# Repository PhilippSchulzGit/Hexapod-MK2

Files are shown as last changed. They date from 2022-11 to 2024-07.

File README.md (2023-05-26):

# Hexapod_MK2
CAD and Code for my second iteration of a hexapod robot.

Check the video on YouTube for more detailed information: https://youtu.be/Rfa3LTjmms0

Update 2023:
This repository also contains the program files for the inverse kinematic model in its own sub folder. Video: https://youtu.be/MJIe1nkX_Xk

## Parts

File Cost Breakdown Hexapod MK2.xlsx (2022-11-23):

Category | Part | Time | Filament [g] | Count | Price | Sum
 |  |  |  |  |  |  | time | filament | price
3D Prints | TorsoV1 | 11:51:00 | 64 | 1 | 1.88 € | 6.28 € | 0.49375 | 64 | 1.88
 | TorsoServoMountV1 | 4:19:00 | 25 | 6 | 0.10 € |  | 1.079166667 | 150 | 0.62
 | LegHipV2 | 11:06:00 | 84 | 6 | 0.35 € |  | 2.775 | 504 | 2.08
 | LegMiddleV1 | 6:31:00 | 27 | 6 | 0.11 € |  | 1.629166667 | 162 | 0.66
 | LegTipV1 | 7:09:00 | 42 | 6 | 0.17 € |  | 1.7875 | 252 | 1.04
Electronics | 9g Servo (https://www.amazon.de/gp/product/B07KFXYDHF/) | - | - | 18 | 1.75 € | 82.14 € |  |  | 31.5
 | PCA 9685 PWM Board (https://www.amazon.de/gp/product/B07CRDCP8V/) | - | - | 1 | 3.33 € |  |  |  | 3.33
 | RC Servo Cable Extensions (https://www.amazon.de/gp/product/B082Y4QK9J/) | - | - | 1 | 9.99 € |  |  |  | 9.99
 | ESP 8266 NodeMCU V2 (https://www.amazon.de/dp/B06Y1LZLLY/) | - | - | 1 | 7.49 € |  |  |  | 7.49
 | GY-521 MPU-6050 (https://www.amazon.de/gp/product/B07TKLYBD6/) | - | - | 1 | 4.79 € |  |  |  | 4.79
 | Mini 360 Buck Converter (https://www.amazon.de/gp/product/B07DK64L2J/) | - | - | 4 | 1.50 € |  |  |  | 5.99
 | 3S 11,1V 2200mAh LiPo Battery (https://www.amazon.de/gp/product/B07LFSPQM2/) | - | - | 1 | 19.05 € |  |  |  | 19.05
 |  |  |  |  | Sum | 88.42 €

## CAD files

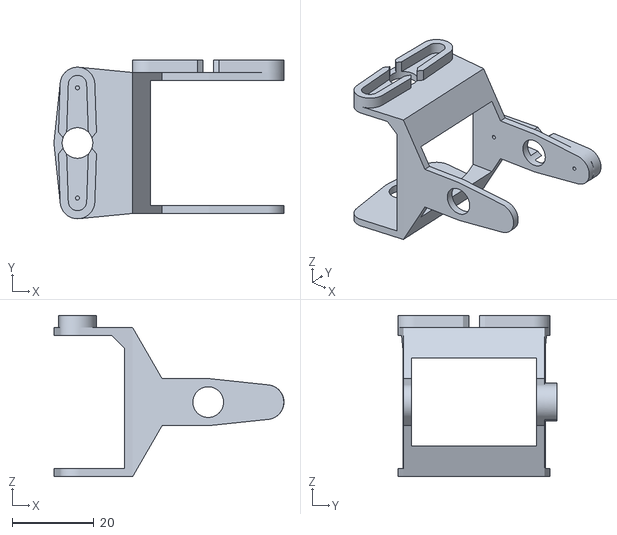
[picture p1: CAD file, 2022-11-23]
CAD/LegHipV2.stl
56.3 x 38.8 x 39.5

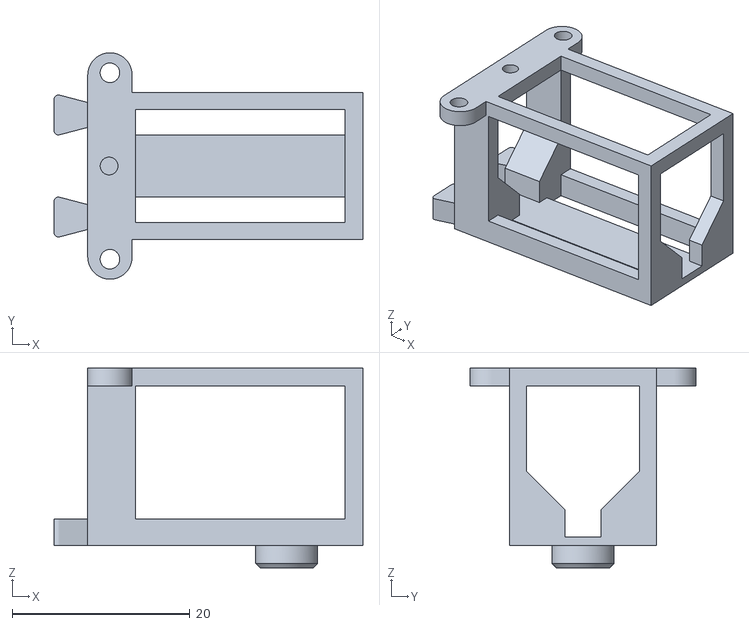
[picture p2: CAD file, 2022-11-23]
CAD/TorsoServoMountV1.stl
34.8 x 25.5 x 22.5

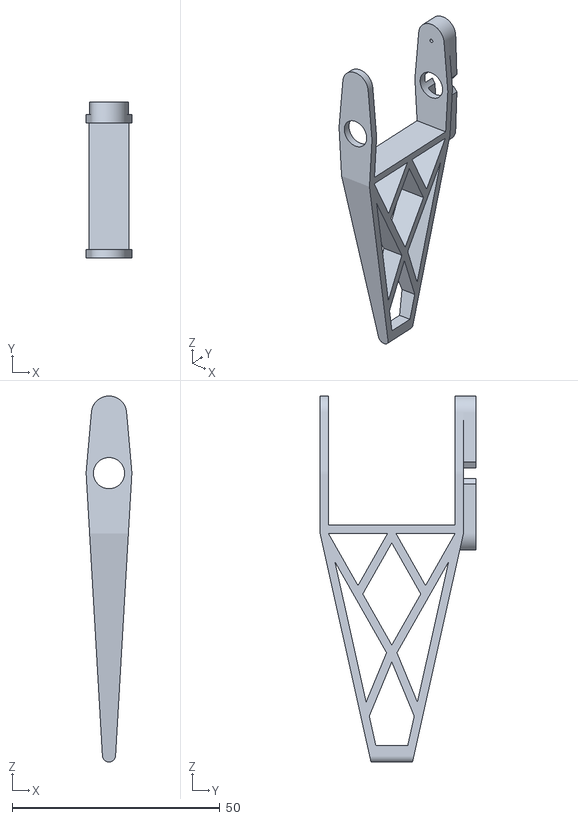
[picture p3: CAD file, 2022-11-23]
CAD/LegTipV1.stl
11.0 x 37.5 x 88.1

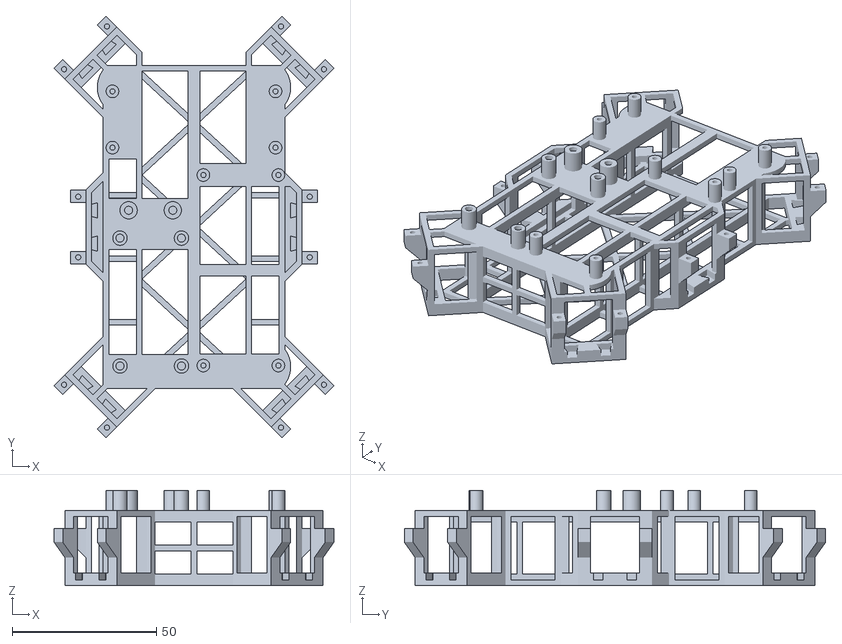
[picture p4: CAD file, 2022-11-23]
CAD/TorsoV1.stl
97.0 x 146.0 x 33.0

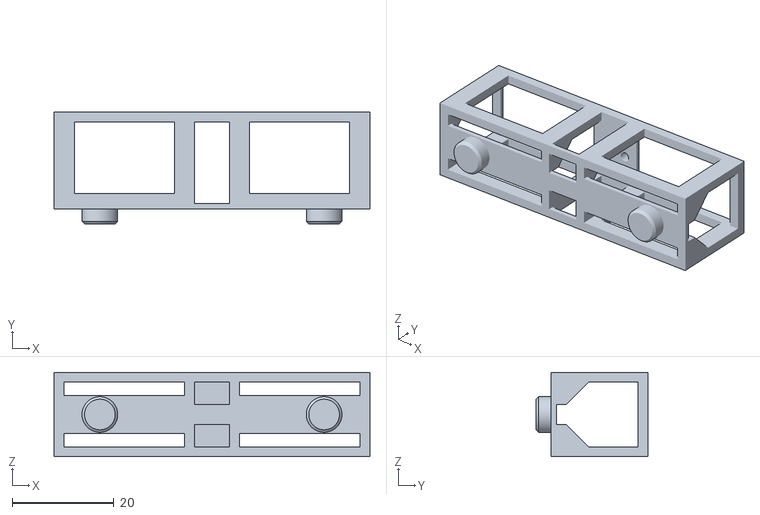
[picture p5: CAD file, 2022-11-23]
CAD/LegMiddleV1.stl
62.0 x 22.0 x 16.5

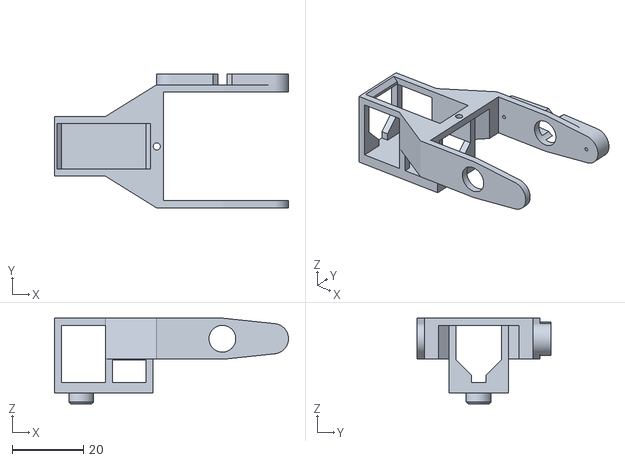
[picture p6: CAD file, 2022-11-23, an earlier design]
CAD/LegHipV1.stl
65.6 x 37.5 x 24.0

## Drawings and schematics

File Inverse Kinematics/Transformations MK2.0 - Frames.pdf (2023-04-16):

# Transformation MK2.0 - Frames

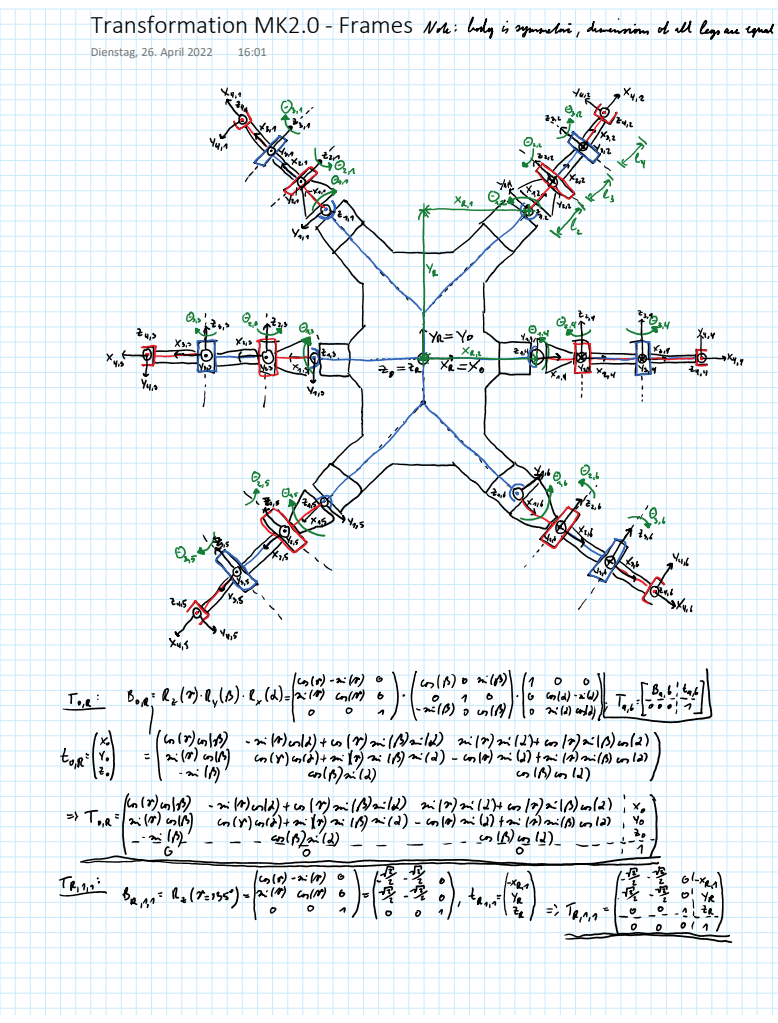
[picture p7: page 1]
Dienstag, 26. April 2022

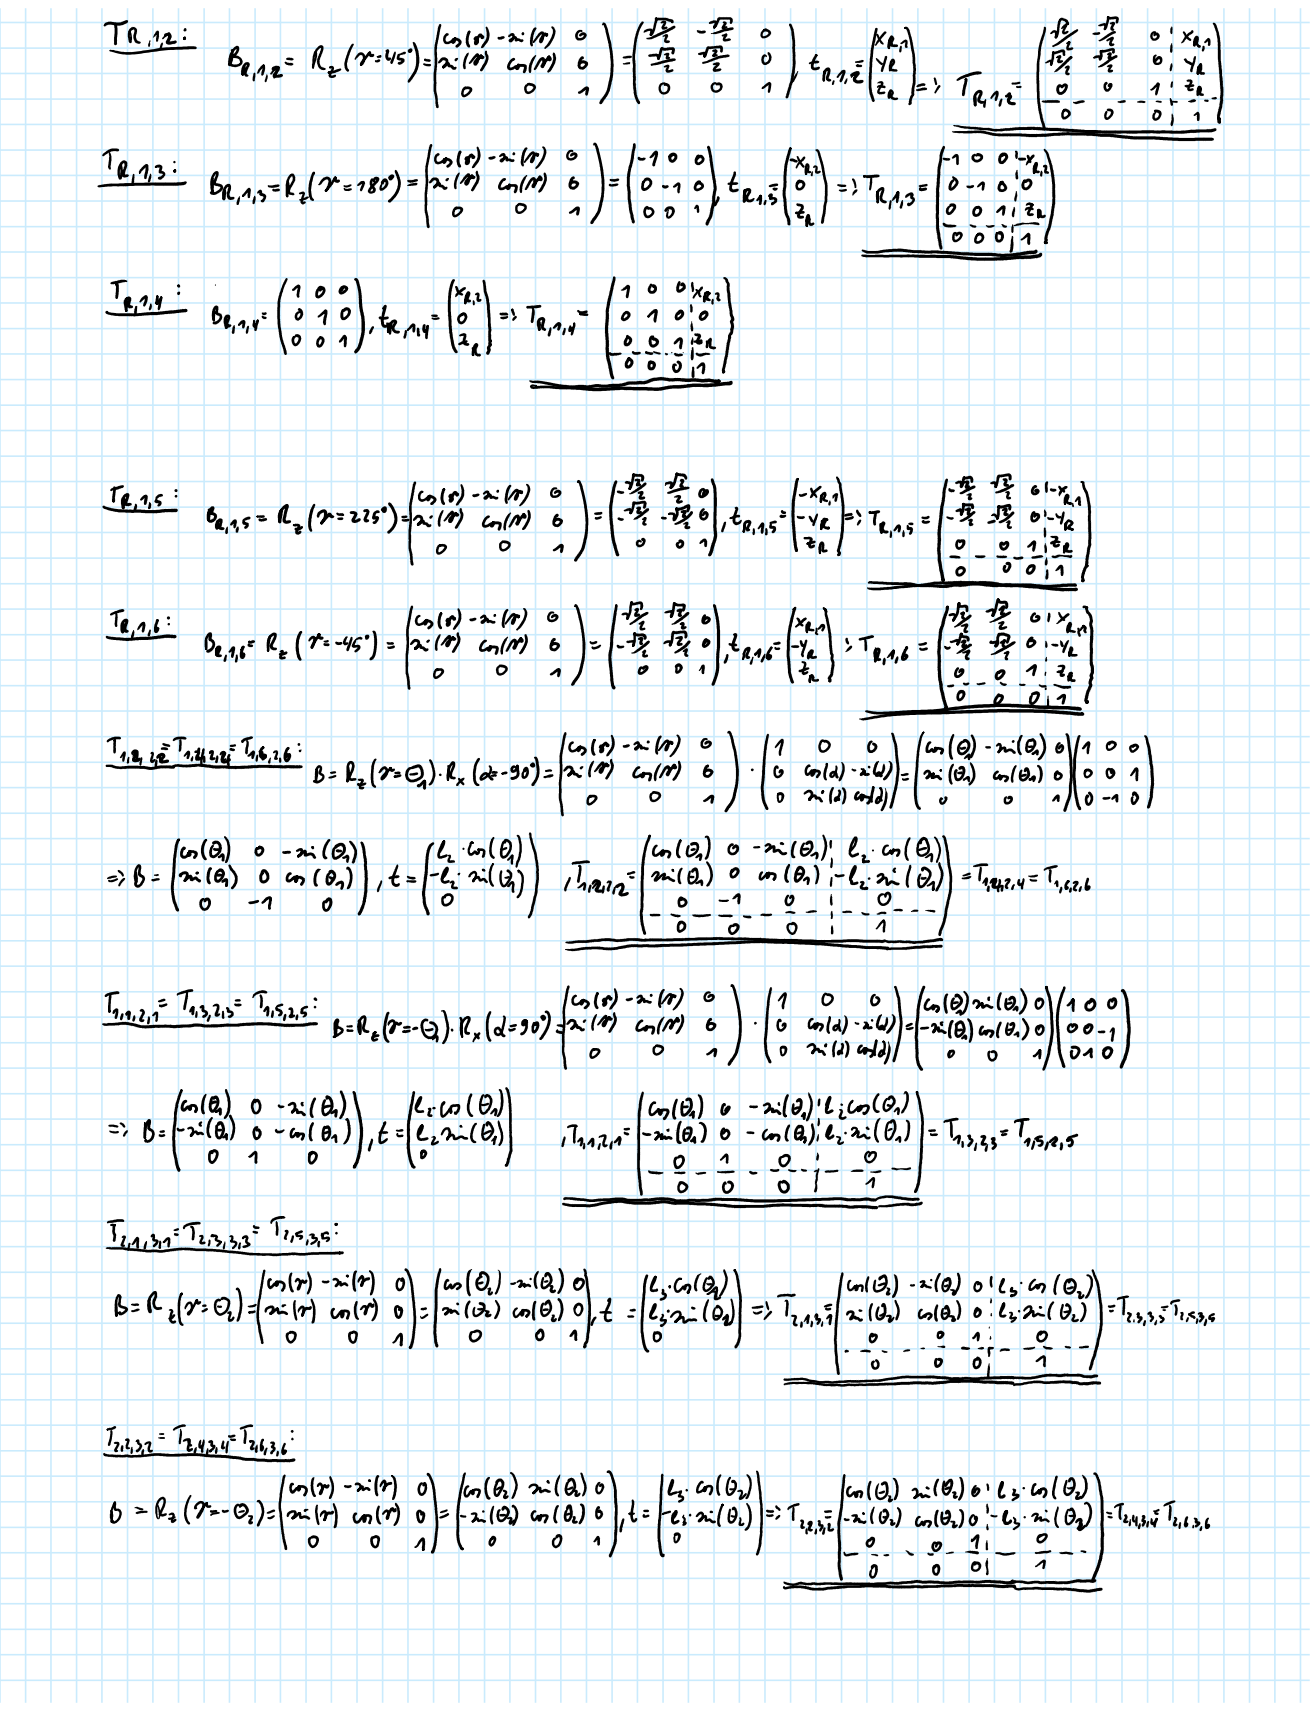
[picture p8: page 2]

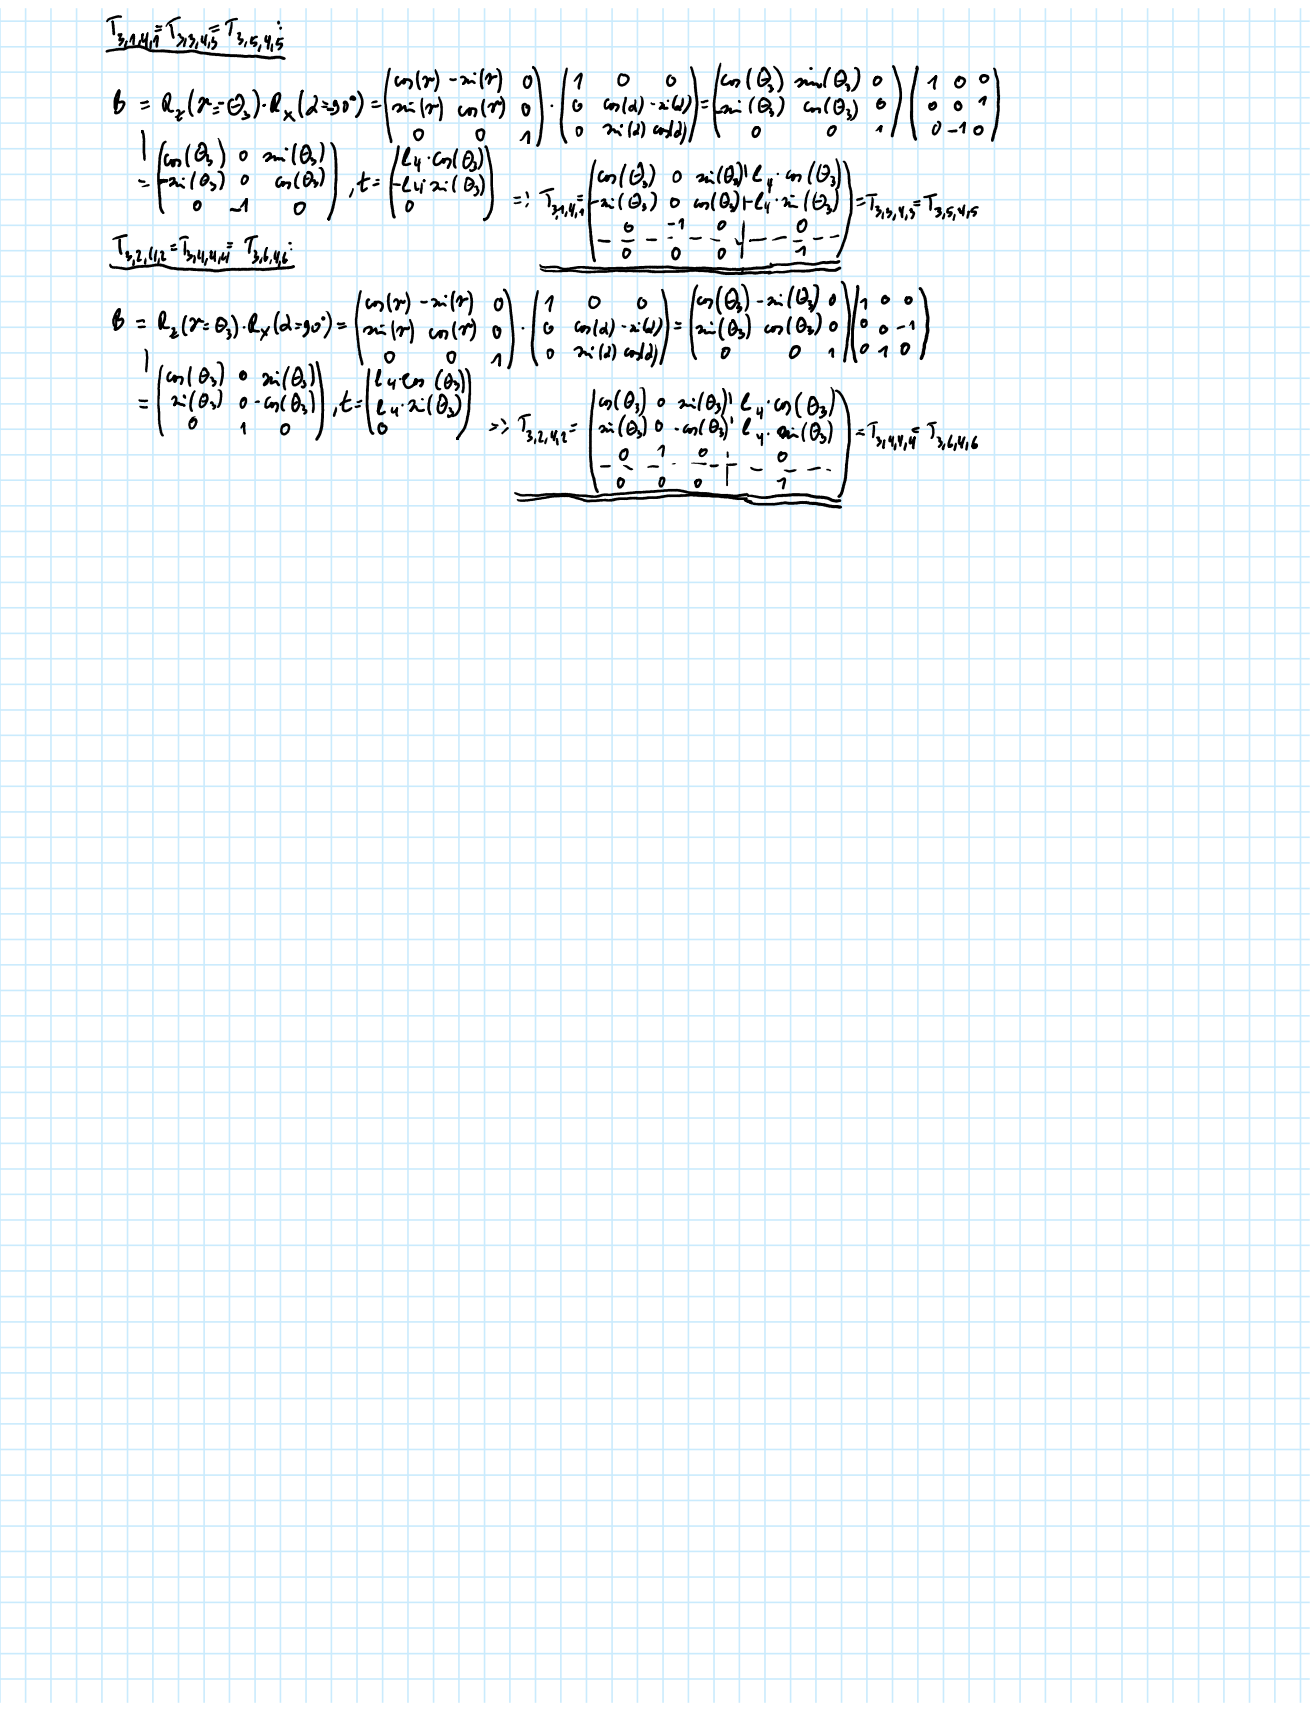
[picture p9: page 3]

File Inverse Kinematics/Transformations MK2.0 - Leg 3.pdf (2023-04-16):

# Transformation MK2.0 - Leg 3

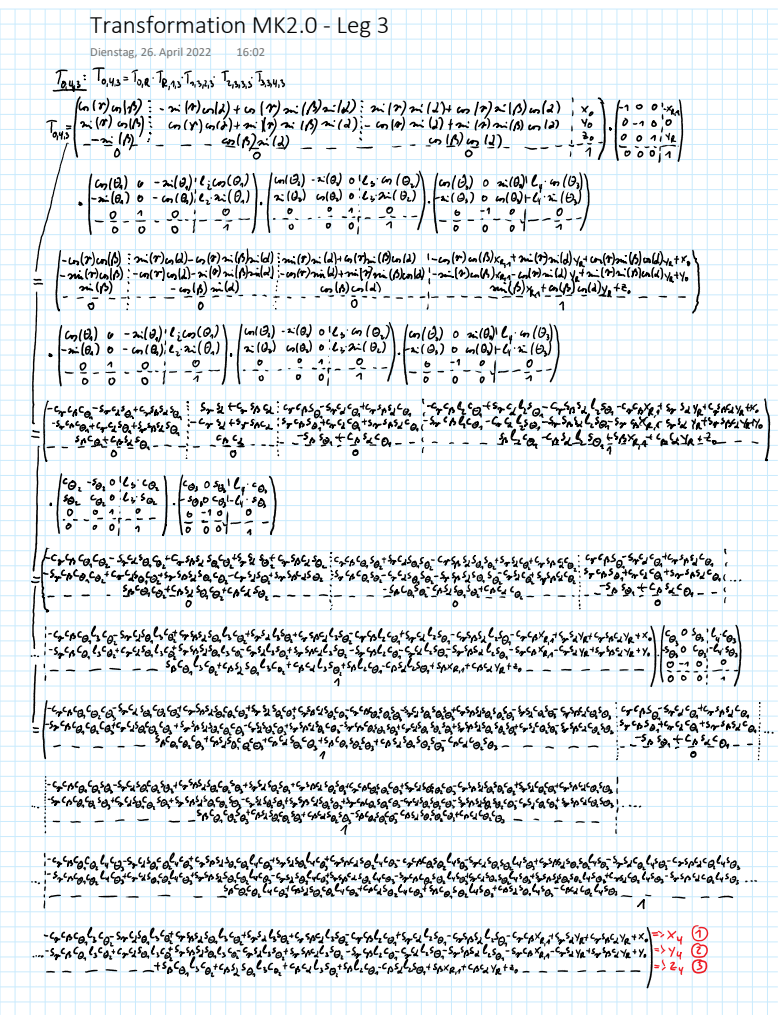
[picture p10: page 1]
Dienstag, 26. April 2022

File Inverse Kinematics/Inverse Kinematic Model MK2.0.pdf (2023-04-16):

# IKM MK2.0

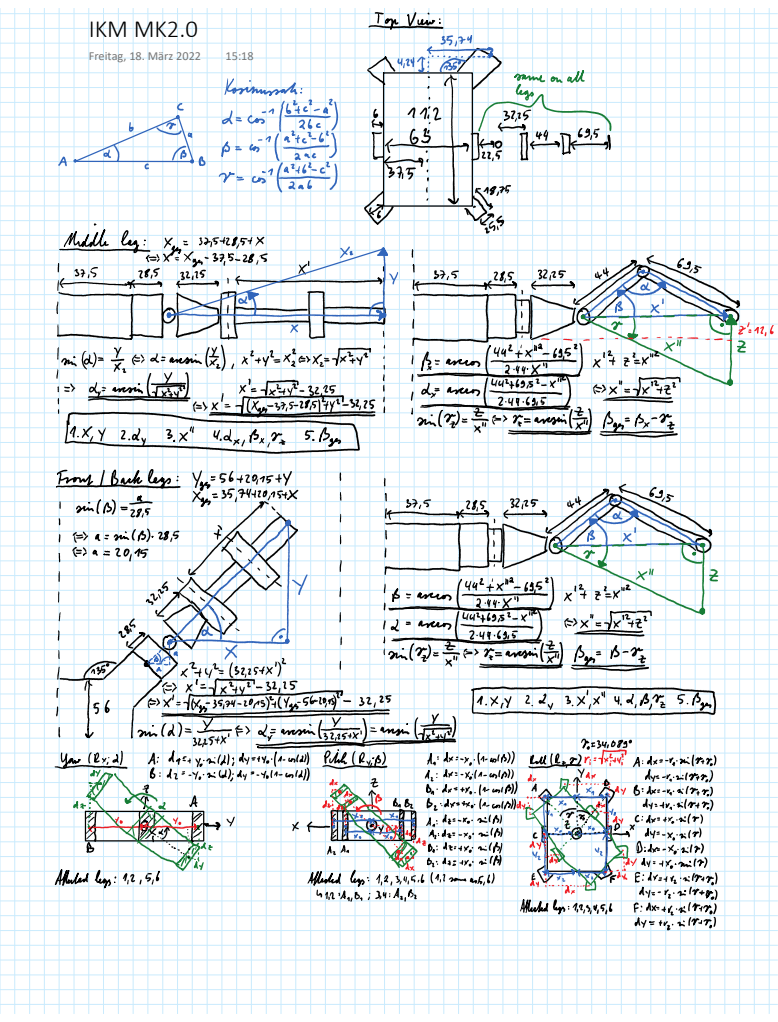
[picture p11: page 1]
Freitag, 18. März 2022

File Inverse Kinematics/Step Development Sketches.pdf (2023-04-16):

# Step Development Sketches

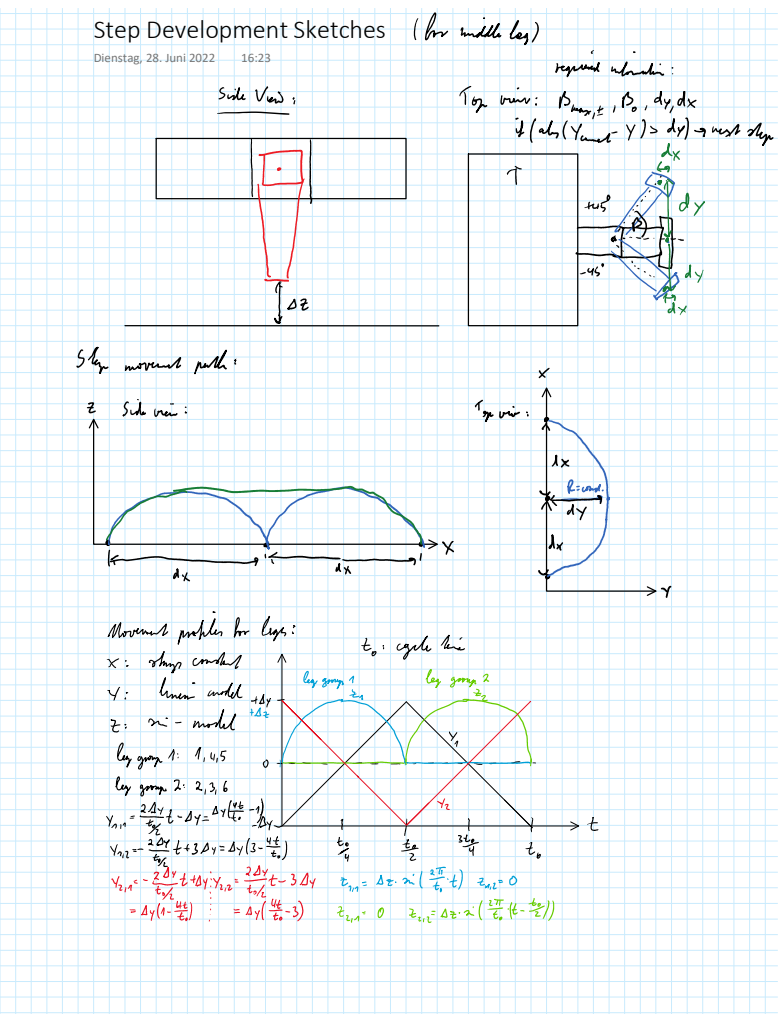
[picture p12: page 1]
Dienstag, 28. Juni 2022

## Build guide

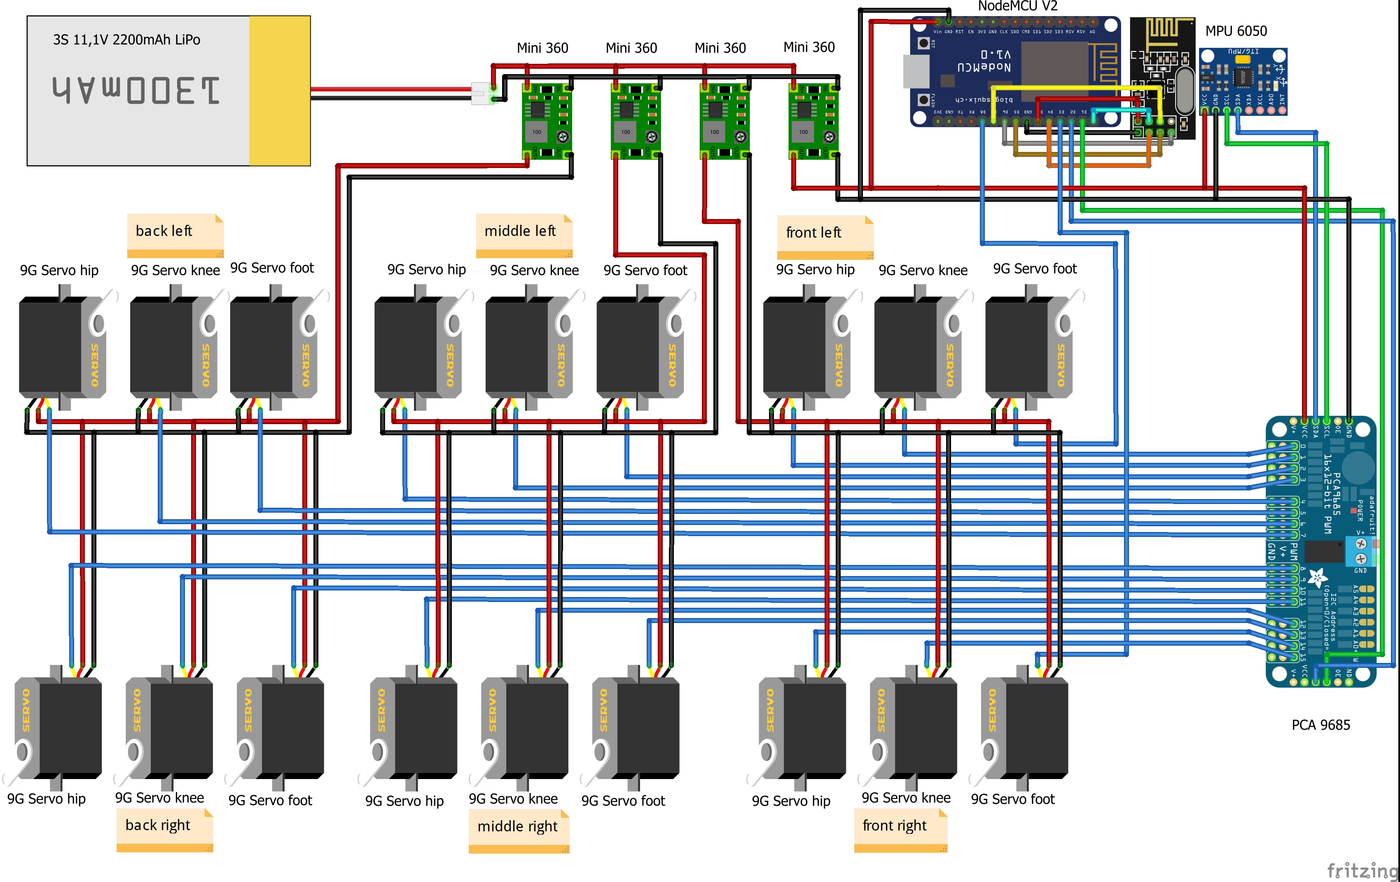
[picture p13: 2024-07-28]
Electrical Documents/Hexapod MK2 Wiring Diagram.jpg

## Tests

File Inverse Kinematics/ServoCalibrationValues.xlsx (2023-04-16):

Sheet: Hips
leg number | servo number | +90° | 0° | -90° | m | b | 90 | 0 | -90
1 | 1 | 0 | 90 | 180 | -1 | 90 | 0 | 90 | 180
2 | 4 | 180 | 90 | 0 | 1 | 90 | 180 | 90 | 0
3 | 7 | 0 | 90 | 180 | -1 | 90 | 0 | 90 | 180
4 | 10 | 180 | 90 | 0 | 1 | 90 | 180 | 90 | 0
5 | 13 | 0 | 90 | 180 | -1 | 90 | 0 | 90 | 180
6 | 16 | 180 | 90 | 0 | 1 | 90 | 180 | 90 | 0
 |  | measurements |  |  | linear equation param |  | test values

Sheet: Knees
leg number | servo number | +90° | 0° | -90° | m | b | 90 | 0 | -90
1 | 2 | 180 | 90 | 0 | 1 | 90 | 180 | 90 | 0
2 | 5 | 180 | 90 | 0 | 1 | 90 | 180 | 90 | 0
3 | 8 | 180 | 90 | 0 | 1 | 90 | 180 | 90 | 0
4 | 11 | 180 | 90 | 0 | 1 | 90 | 180 | 90 | 0
5 | 14 | 180 | 90 | 0 | 1 | 90 | 180 | 90 | 0
6 | 17 | 180 | 90 | 0 | 1 | 90 | 180 | 90 | 0
 |  | measurements |  |  | linear equation param |  | test values
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

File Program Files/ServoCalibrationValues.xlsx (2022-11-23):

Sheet: Hips
leg number | servo number | +90° | 0° | -90° | m | b | 90 | 0 | -90
1 | 1 | 0 | 90 | 180 | -1 | 90 | 0 | 90 | 180
2 | 4 | 180 | 90 | 0 | 1 | 90 | 180 | 90 | 0
3 | 7 | 0 | 90 | 180 | -1 | 90 | 0 | 90 | 180
4 | 10 | 180 | 90 | 0 | 1 | 90 | 180 | 90 | 0
5 | 13 | 0 | 90 | 180 | -1 | 90 | 0 | 90 | 180
6 | 16 | 180 | 90 | 0 | 1 | 90 | 180 | 90 | 0
 |  | measurements |  |  | linear equation param |  | test values

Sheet: Knees
leg number | servo number | +90° | 0° | -90° | m | b | 90 | 0 | -90
1 | 2 | 180 | 90 | 0 | 1 | 90 | 180 | 90 | 0
2 | 5 | 180 | 90 | 0 | 1 | 90 | 180 | 90 | 0
3 | 8 | 180 | 90 | 0 | 1 | 90 | 180 | 90 | 0
4 | 11 | 180 | 90 | 0 | 1 | 90 | 180 | 90 | 0
5 | 14 | 180 | 90 | 0 | 1 | 90 | 180 | 90 | 0
6 | 17 | 180 | 90 | 0 | 1 | 90 | 180 | 90 | 0
 |  | measurements |  |  | linear equation param |  | test values
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

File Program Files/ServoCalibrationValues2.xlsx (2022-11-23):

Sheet: Hips
leg number | servo number | +90° | 0° | -90° | m | b | 90 | 0 | -90
1 | 1 | 0 | 90 | 180 | -1 | 90 | 0 | 90 | 180
2 | 4 | 180 | 90 | 0 | 1 | 90 | 180 | 90 | 0
3 | 7 | 0 | 90 | 180 | -1 | 90 | 0 | 90 | 180
4 | 10 | 180 | 90 | 0 | 1 | 90 | 180 | 90 | 0
5 | 13 | 0 | 90 | 180 | -1 | 90 | 0 | 90 | 180
6 | 16 | 180 | 90 | 0 | 1 | 90 | 180 | 90 | 0
 |  | measurements |  |  | linear equation param |  | test values

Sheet: Knees
leg number | servo number | +90° | 0° | -90° | m | b | 90 | 0 | -90
1 | 2 | 180 | 90 | 0 | 1 | 90 | 180 | 90 | 0
2 | 5 | 180 | 90 | 0 | 1 | 90 | 180 | 90 | 0
3 | 8 | 180 | 90 | 0 | 1 | 90 | 180 | 90 | 0
4 | 11 | 180 | 90 | 0 | 1 | 90 | 180 | 90 | 0
5 | 14 | 180 | 90 | 0 | 1 | 90 | 180 | 90 | 0
6 | 17 | 180 | 90 | 0 | 1 | 90 | 180 | 90 | 0
 |  | measurements |  |  | linear equation param |  | test values
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

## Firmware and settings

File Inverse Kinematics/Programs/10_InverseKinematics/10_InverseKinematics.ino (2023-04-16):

/**
 * Program to test out the proper inverse kinematic model plus remote usage
 * Created:   23.03.2023
 * Modified:  05.04.2023
 * Author:    Philipp Schulz
 */
#include <Wire.h>
// ---------------NRF24L01-----------
#include <SPI.h>
#include <RF24.h>
// ---------------NRF24L01-----------
#include <Adafruit_PWMServoDriver.h>
#include <Servo.h>
Adafruit_PWMServoDriver pwmBoard = Adafruit_PWMServoDriver(0x41);   //object of the pwm driver board
Servo S1;         // Servo object 1
Servo S2;         // Servo object 2

#define FREQUENCY 50

#define SERVOMIN  697  // This is the 'minimum' pulse length count (out of 4096)
#define SERVOMAX  2741 // This is the 'maximum' pulse length count (out of 4096)

// --------------------------used PWM pins on boards----------------------
/* Servo Nr. | Leg Nr. | Location  | Direction | Joint | Connection | Pin Nr.
       1     |    1    |   front   |    left   |  hip  | PWM Board  |    1
       2     |    1    |   front   |    left   | knee  | PWM Board  |    0
       3     |    1    |   front   |    left   | foot  |    MCU     |   PWM1/5
       4     |    2    |   front   |   right   |  hip  | PWM Board  |    15
       5     |    2    |   front   |   right   | knee  | PWM Board  |    14
       6     |    2    |   front   |   right   | foot  |    MCU     |   PWM2/6
       7     |    3    |  middle   |    left   |  hip  | PWM Board  |    4
       8     |    3    |  middle   |    left   | knee  | PWM Board  |    3
       9     |    3    |  middle   |    left   | foot  | PWM Board  |    2
      10     |    4    |  middle   |   right   |  hip  | PWM Board  |    11
      11     |    4    |  middle   |   right   | knee  | PWM Board  |    12
      12     |    4    |  middle   |   right   | foot  | PWM Board  |    13
      13     |    5    |   back    |    left   |  hip  | PWM Board  |    7
      14     |    5    |   back    |    left   | knee  | PWM Board  |    6
      15     |    5    |   back    |    left   | foot  | PWM Board  |    5
      16     |    6    |   back    |   right   |  hip  | PWM Board  |    8
      17     |    6    |   back    |   right   | knee  | PWM Board  |    9
      18     |    6    |   back    |   right   | foot  | PWM Board  |    10
// --------------------------used PWM pins on boards----------------------*/

// servo calibration values
//s:          1  2  3  4  5  6          7  8  9 10 11 12 13 14 15 16 17 18
float m[] = {-1, 1, 1, 1, 1, 0.833333 ,-1, 1, 1, 1, 1, 1,-1, 1, 1, 1, 1, 1};
float b[] = {90,90,45,90,90, 35.5,     90,90,45,90,90,45,90,90,45,90,90,45};
                     // 1  2  3  4  5  6  7  8  9 10 11 12 13 14 15 16 17 18
float servoValues[] = { 0, 0, 0, 0, 0, 0, 0, 0, 0, 0, 0, 0, 0, 0, 0, 0, 0, 0};

// default translation and rotation for any leg, any additional input will be added to these values
float defaultLegTransform[] = {44,0,-69.5,0,0,0}; // x y z alpha beta gamma

// variables for homing
long startAngle = 0;
int homingDelay = 250;

//variables for movement patterns
int cycleTime = 10;

// for controlling loop times
int servoLoopTime = 10;  // ms
long lastTimestamp = 0;
// variables for IKM
float kartesian[] = {0,0,0,0,0,0};  // x y z alpha beta gamma, transform from global to robot coordinate system!
// servo angles from inverse kinematics 1  2  3  4  5  6  7  8  9 10 11 12 13 14 15 16 17 18
float kartesianAngles[] =             { 0, 0, 0, 0, 0, 0, 0, 0, 0, 0, 0, 0, 0, 0, 0, 0, 0, 0};
// reference positions required for walking
float kartesianRef[][3] =              { {0, 0, 0}, {0, 0, 0}, {0, 0, 0}, {0, 0, 0}, {0, 0, 0}, {0, 0, 0}};
// x coordinates for inverse kinematics 1  2  3  4  5  6
float kartesianX[] =                  { 0, 0, 0, 0, 0, 0};
// y coordinates for inverse kinematics 1  2  3  4  5  6
float kartesianY[] =                  { 0, 0, 0, 0, 0, 0};
// z coordinates for inverse kinematics 1  2  3  4  5  6
float kartesianZ[] =                  { 0, 0, 0, 0, 0, 0};
// ---------------NRF24L01-----------
// variables for all IO
byte leds[] = {0,0,0,0,0}; // led1, led2, led3, led4, led5
byte switches[] = {0,0,0,0,0};   // sw1, sw2, sw3, sw4, sw5
byte switchesPrev[] = {0,0,0,0,0};   // sw1, sw2, sw3, sw4, sw5
byte buttons[] = {0,0,0,0,0,0};  // L1, L2, StickL, R1, R2, StickR
int axes[] = {0,0,0,0,0,0};      // Lx, Ly, Lz, Rx, Ry, Rz

// -------walking constants-------
const float yDelta = 20;
const float zDelta = 30;
const float stepTime = 2000;   // seconds
const int indices1[] = {0,3,4};
const int indices2[] = {1,2,5};
long walkingTimestamp = 0;
// phases for set walking demo
float walkingPhases[] = {stepTime/2, stepTime/2, stepTime/2, stepTime/2, stepTime/2, stepTime/2};  

// ----------inverse kinematics--------------
const float y00 = 56+4.24;
const float x0 = 31.5;
const float x1 = 35.74;
const float l1m = 32.25;
const float l0m = 28.5;
const float l0o = 20.15;
const float l1corr = 0.09;
const float l2 = 44;
const float l3 = 69.5;

// structure for data to send to client device
struct SEND_DATA_STRUCTURE_OPTIMIZED{
    byte buttons;
    byte switches;
    int16_t rx_left;
    int16_t ry_left;
    int16_t rz_left;
    int16_t rx_right;
    int16_t ry_right;
    int16_t rz_right;
};
// structure for data to receive from client device
struct RECEIVE_DATA_STRUCTURE_OPTIMIZED{
  byte leds;
};
// create objects of structures
SEND_DATA_STRUCTURE_OPTIMIZED dataToSend;
RECEIVE_DATA_STRUCTURE_OPTIMIZED dataToRead;
// initialize the NRF24L01 chip
RF24 radio(2, 16); // CE, CSN
// addresses for sender and receiver
const byte addresses[][6] = {"01", "02"};
// ---------------NRF24L01-----------
//converts given angle to a number in 4096 for the PWM board
int pulseWidth(int angle){          
  int pulse_wide, analog_value;
  pulse_wide = map(angle, 0, 180, SERVOMIN, SERVOMAX);
  analog_value = int(float(pulse_wide) / 1000000 * FREQUENCY * 4096);
  return analog_value;
}

// https://stackoverflow.com/questions/9072320/split-string-into-string-array
String getValue(String data, char separator, int index)
{
  int found = 0;
  int strIndex[] = {0, -1};
  int maxIndex = data.length()-1;

  for(int i=0; i<=maxIndex && found<=index; i++){
    if(data.charAt(i)==separator || i==maxIndex){
        found++;
        strIndex[0] = strIndex[1]+1;
        strIndex[1] = (i == maxIndex) ? i+1 : i;
    }
  }

  return found>index ? data.substring(strIndex[0], strIndex[1]) : "";
}

// ---------------NRF24L01-----------
// method for setting the data from global variables to be sent
void setPayloadContent() {
  byte ledsByte = 0;
  for(int i=0;i<6;i++) {
    if(leds[i]) {
      ledsByte |= (1 << (7-i));
    }
  }
  dataToRead.leds = ledsByte;
}

// method for getting the received data to global variables
void getPayloadContent() {
  for(int i=0;i<6;i++) {
    buttons[i] = bitRead(dataToSend.buttons, (7-i));
  }
  for(int i=0;i<5;i++) {
    switches[i] = bitRead(dataToSend.switches, (7-i));
  }
  axes[0] = dataToSend.rx_left;
  axes[1] = dataToSend.ry_left;
  axes[2] = dataToSend.rz_left;
  axes[3] = dataToSend.rx_right;
  axes[4] = dataToSend.ry_right;
  axes[5] = dataToSend.rz_right;
}

// method for handling all radio related code
void handleRadio() {
  uint8_t pipe;
  // check if radio has a new payload
  if (radio.available(&pipe)) { 
    // get dynamic payload size
    uint8_t bytes = radio.getDynamicPayloadSize();
    // read data
    radio.read(&dataToSend, sizeof(dataToSend));
    // handle payload
    getPayloadContent();
    // prepare return payload
    setPayloadContent();
    // send ack ACK payload
    radio.writeAckPayload(1,&dataToRead,sizeof(dataToRead));
  }
}
// ---------------NRF24L01-----------

// method to utilize servo calibration values
float servoCalibration(int servoNumber, float targetPosition) {
  return m[servoNumber-1]*targetPosition + b[servoNumber-1];  // return value based on calibration
}


// method to set a servo by its number to a new targetPosition
void setServoByNumber(int servoNumber, float targetPosition) {
  switch(servoNumber) {                                   // go over all possible servo numbers
    case 1:
      pwmBoard.setPWM(1,0,pulseWidth(servoCalibration(servoNumber,targetPosition)));    // move servo 1 in position
      break;
    case 2:
      pwmBoard.setPWM(0,0,pulseWidth(servoCalibration(servoNumber,targetPosition)));    // move servo 2 in position
      break;
    case 3:
      S1.write(servoCalibration(servoNumber,targetPosition));                           // move servo 3 in position
      break;
    case 4:
      pwmBoard.setPWM(15,0,pulseWidth(servoCalibration(servoNumber,targetPosition)));   // move servo 4 in position
      break;
    case 5:
      pwmBoard.setPWM(14,0,pulseWidth(servoCalibration(servoNumber,targetPosition)));   // move servo 5 in position
      break;
    case 6:
      S2.write(servoCalibration(servoNumber,targetPosition));                           // move servo 6 in position
      break;
    case 7:
      pwmBoard.setPWM(4,0,pulseWidth(servoCalibration(servoNumber,targetPosition)));    // move servo 7 in position
      break;
    case 8:
      pwmBoard.setPWM(3,0,pulseWidth(servoCalibration(servoNumber,targetPosition)));    // move servo 8 in position
      break;
    case 9:
      pwmBoard.setPWM(2,0,pulseWidth(servoCalibration(servoNumber,targetPosition)));    // move servo 9 in position
      break;
    case 10:
      pwmBoard.setPWM(11,0,pulseWidth(servoCalibration(servoNumber,targetPosition)));   // move servo 10 in position
      break;
    case 11:
      pwmBoard.setPWM(12,0,pulseWidth(servoCalibration(servoNumber,targetPosition)));   // move servo 11 in position
      break;
    case 12:
      pwmBoard.setPWM(13,0,pulseWidth(servoCalibration(servoNumber,targetPosition)));   // move servo 12 in position
      break;
    case 13:
      pwmBoard.setPWM(7,0,pulseWidth(servoCalibration(servoNumber,targetPosition)));    // move servo 13 in position
      break;
    case 14:
      pwmBoard.setPWM(6,0,pulseWidth(servoCalibration(servoNumber,targetPosition)));    // move servo 14 in position
      break;
    case 15:
      pwmBoard.setPWM(5,0,pulseWidth(servoCalibration(servoNumber,targetPosition)));    // move servo 15 in position
      break;
    case 16:
      pwmBoard.setPWM(8,0,pulseWidth(servoCalibration(servoNumber,targetPosition)));    // move servo 16 in position
      break;
    case 17:
      pwmBoard.setPWM(9,0,pulseWidth(servoCalibration(servoNumber,targetPosition)));    // move servo 17 in position
      break;
    case 18:
      pwmBoard.setPWM(10,0,pulseWidth(servoCalibration(servoNumber,targetPosition)));   // move servo 18 in position
      break;
  }
  // save current position for movement commands
  servoValues[servoNumber-1] = targetPosition;
}

// method to determine direction of offset for movements
int determineIncrement(int current,int target,int incrementSize) {
  // check if the delta is positive or negative, return the given increment in the fitting direction
  if((current-target) > 0 ) { // if the target is smaller than the current position
    return -incrementSize;
  } else {                    // if the target is larger than the current position
    return incrementSize;
  }
}

//  method to move all servos so that the hexapod stands up
void standUp() {
  // 1. all hips 0°
  // 2. all knees 30°
  // 3. all feet 90°
  // 4. all knees 0°

  // placeholder condition for overall step conditions
  boolean condition = false;

  // phase 1: loop until all hips are in position
  int target = 0;
  while(!condition) {
    // check hip 1 and adjust the saved values for the required movement
    if(servoValues[0]!=target) {
      servoValues[0] = servoValues[0]+determineIncrement(servoValues[0],target,1);
      setServoByNumber(1,servoValues[0]);
    }
    // check hip 2 and adjust the saved values for the required movement
    if(servoValues[3]!=target) {
      servoValues[3] = servoValues[3]+determineIncrement(servoValues[3],target,1);
      setServoByNumber(4,servoValues[3]);
    }
    // check hip 3 and adjust the saved values for the required movement
    if(servoValues[6]!=target) {
      servoValues[6] = servoValues[6]+determineIncrement(servoValues[6],target,1);
      setServoByNumber(7,servoValues[6]);
    }
    // check hip 4 and adjust the saved values for the required movement
    if(servoValues[9]!=target) {
      servoValues[9] = servoValues[9]+determineIncrement(servoValues[9],target,1);
      setServoByNumber(10,servoValues[9]);
    }
    // check hip 5 and adjust the saved values for the required movement
    if(servoValues[12]!=target) {
      servoValues[12] = servoValues[12]+determineIncrement(servoValues[12],target,1);
      setServoByNumber(13,servoValues[12]);
    }
    // check hip 6 and adjust the saved values for the required movement
    if(servoValues[15]!=target) {
      servoValues[15] = servoValues[15]+determineIncrement(servoValues[15],target,1);
      setServoByNumber(16,servoValues[15]);
    }
    // check if the condition is met
    if(servoValues[0]==target && servoValues[3]==target && servoValues[6]==target && servoValues[9]==target && servoValues[12]==target && servoValues[15]==target) {
      condition = true;
    }
    // wait for loop cycle time
    delay(cycleTime);
  }
  // phase 2: loop until all knees are in position
  target = 30;
  condition = false;
  while(!condition) {
    // check knee 1 and adjust the saved values for the required movement
    if(servoValues[1]!=target) {
      servoValues[1] = servoValues[1]+determineIncrement(servoValues[1],target,1);
      setServoByNumber(2,servoValues[1]);
    }
    // check knee 2 and adjust the saved values for the required movement
    if(servoValues[4]!=target) {
      servoValues[4] = servoValues[4]+determineIncrement(servoValues[4],target,1);
      setServoByNumber(5,servoValues[4]);
    }
    // check knee 3 and adjust the saved values for the required movement
    if(servoValues[7]!=target) {
      servoValues[7] = servoValues[7]+determineIncrement(servoValues[7],target,1);
      setServoByNumber(8,servoValues[7]);
    }
    // check knee 4 and adjust the saved values for the required movement
    if(servoValues[10]!=target) {
      servoValues[10] = servoValues[10]+determineIncrement(servoValues[10],target,1);
      setServoByNumber(11,servoValues[10]);
    }
    // check knee 5 and adjust the saved values for the required movement
    if(servoValues[13]!=target) {
      servoValues[13] = servoValues[13]+determineIncrement(servoValues[13],target,1);
      setServoByNumber(14,servoValues[13]);
    }
    // check knee 6 and adjust the saved values for the required movement
    if(servoValues[16]!=target) {
      servoValues[16] = servoValues[16]+determineIncrement(servoValues[16],target,1);
      setServoByNumber(17,servoValues[16]);
    }
    // check if the condition is met
    if(servoValues[1]==target && servoValues[4]==target && servoValues[7]==target && servoValues[10]==target && servoValues[13]==target && servoValues[16]==target) {
      condition = true;
    }
    // wait for loop cycle time
    delay(cycleTime);
  }
  // phase 3: loop until all feet are in position
  target = 90;
  condition = false;
  while(!condition) {
    // check foot 1 and adjust the saved values for the required movement
    if(servoValues[2]!=target) {
      servoValues[2] = servoValues[2]+determineIncrement(servoValues[2],target,1);
      setServoByNumber(3,servoValues[2]);
    }
    // check foot 2 and adjust the saved values for the required movement
    if(servoValues[5]!=target) {
      servoValues[5] = servoValues[5]+determineIncrement(servoValues[5],target,1);
      setServoByNumber(6,servoValues[5]);
    }
    // check foot 3 and adjust the saved values for the required movement
    if(servoValues[8]!=target) {
      servoValues[8] = servoValues[8]+determineIncrement(servoValues[8],target,1);
      setServoByNumber(9,servoValues[8]);
    }
    // check foot 4 and adjust the saved values for the required movement
    if(servoValues[11]!=target) {
      servoValues[11] = servoValues[11]+determineIncrement(servoValues[11],target,1);
      setServoByNumber(12,servoValues[11]);
    }
    // check foot 5 and adjust the saved values for the required movement
    if(servoValues[14]!=target) {
      servoValues[14] = servoValues[14]+determineIncrement(servoValues[14],target,1);
      setServoByNumber(15,servoValues[14]);
    }
    // check foot 6 and adjust the saved values for the required movement
    if(servoValues[17]!=target) {
      servoValues[17] = servoValues[17]+determineIncrement(servoValues[17],target,1);
      setServoByNumber(18,servoValues[17]);
    }
    // check if the condition is met
    if(servoValues[2]==target && servoValues[5]==target && servoValues[8]==target && servoValues[11]==target && servoValues[14]==target && servoValues[17]==target) {
      condition = true;
    }
    // wait for loop cycle time
    delay(cycleTime);
  }
  // phase 4: loop until all knees are in position
  target = 0;
  condition = false;
  while(!condition) {
    // check knee 1 and adjust the saved values for the required movement
    if(servoValues[1]!=target) {
      servoValues[1] = servoValues[1]+determineIncrement(servoValues[1],target,1);
      setServoByNumber(2,servoValues[1]);
    }
    // check knee 2 and adjust the saved values for the required movement
    if(servoValues[4]!=target) {
      servoValues[4] = servoValues[4]+determineIncrement(servoValues[4],target,1);
      setServoByNumber(5,servoValues[4]);
    }
    // check knee 3 and adjust the saved values for the required movement
    if(servoValues[7]!=target) {
      servoValues[7] = servoValues[7]+determineIncrement(servoValues[7],target,1);
      setServoByNumber(8,servoValues[7]);
    }
    // check knee 4 and adjust the saved values for the required movement
    if(servoValues[10]!=target) {
      servoValues[10] = servoValues[10]+determineIncrement(servoValues[10],target,1);
      setServoByNumber(11,servoValues[10]);
    }
    // check knee 5 and adjust the saved values for the required movement
    if(servoValues[13]!=target) {
      servoValues[13] = servoValues[13]+determineIncrement(servoValues[13],target,1);
      setServoByNumber(14,servoValues[13]);
    }
    // check knee 6 and adjust the saved values for the required movement
    if(servoValues[16]!=target) {
      servoValues[16] = servoValues[16]+determineIncrement(servoValues[16],target,1);
      setServoByNumber(17,servoValues[16]);
    }
    // check if the condition is met
    if(servoValues[1]==target && servoValues[4]==target && servoValues[7]==target && servoValues[10]==target && servoValues[13]==target && servoValues[16]==target) {
      condition = true;
    }
    // wait for loop cycle time
    delay(cycleTime);
  }
}
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
void loop() {
  // get next set of values
  handleRadio();
  long currentTimestamp = millis();
  if(currentTimestamp-lastTimestamp>servoLoopTime) {
    // save last timestamp
    lastTimestamp = currentTimestamp;
    // process the values
    processVariables();
  }
  // move all servos to targets
  setIKMServos();
}

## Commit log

2022-11-23 Upload of files
    CAD, code and some other files too
    [Cost Breakdown Hexapod MK2.xlsx, LegHipV1.stl, LegHipV2.stl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]
2023-02-17 Electrical documents
    Looks like I forgot to upload the wiring diagram. Oops
    [Hexapod MK2 Wiring Diagram.fzz]
2023-04-16 inverse kinematic model
    - Uploaded sketches, math and programs for inverse kinematic model
    - Updated README
    [ServoCalibrationValues.xlsx]
